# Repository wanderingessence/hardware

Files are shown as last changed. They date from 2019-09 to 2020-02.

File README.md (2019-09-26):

# hardware
Altium repository for pod V. This project is set up to provide all documentation, design and data validation required for the Badgerloop Pod V PCBs. This repository builds off of our previous work the podiv-altium repository. 

## Prerequisites
Altium only works on Windows. See  [Altium System Requirements](https://www.altium.com/documentation/18.0/display/ADES/Altium+Designer+-+((System+Requirements))") for more information. An internet connection is required to connect to the license server and dual monitors are nice to have. Microsoft Excel is required for BOM generation.

## Installation
1. Contact Ezra Boley, Shelby Riggleman or Ryan Castle to be added to the Badgerloop Team AltiumLive Account and the Badgerloop [Github](https://github.com/badgerloop-software"). You will receive an email from Altium with your account information. You may continue to step to step 8 without requiring an active license. If there is a delay for some reason, you can work on Altium training and practice on CAE computers or through [Citrix](https://remote.engr.wisc.edu/vpn/index.html), but we are usually able to add new users within 24 hours. CAE currently runs Altium 16, which has similar features but has a different interface and some bugs. Badgerloop currently supports Altium 19.0.10. 
2. Download the latest version of [Altium Designer](https://www.altium.com/products/downloads) 
3. Install Altium. Default file paths will work.
4. Insall [Git Bash](https://gitforwindows.org/") Git Bash (or whatever BASH emulation tool you are comfortable with)
5. Open Git Bash
6. Type the following commands into the command prompt window:
   + cd ../..
   + mkdir git
   + cd git
   + git clone https://github.com/badgerloop-software/hardware.git
   + cd hardware
   + git checkout -b <your-username_training>
   + Open Altium and sign in. You are now on a training branch that you will complete your first getting started project on if you are new to Altium. 
7. Go to User (Silhouette in the top right corner) -> License Management. Then Click Sign In and enter your username and password associated with Altium Live and accept the warning. It's also a good idea to check Sign me in when I start Altium Designer if you'd like to save a little time.

_NOTE: If you go click "Sign In" directly from User, you will be asked for a server address. This is not what you want. Go back to step 7 and hit License Management instead of Sign In._ 

8. Click Use to claim a license. If you are not using a valid license, you will be able to view files in Altium Designer but you will not be able to make edits. Ensure that you are choosing an Altium Designer License and not our PDN License. That's something else. 
9. You are now ready to use Altium. See [Training](#training) for more details on how to get started. 

## Training
+ View the [Badgerloop Altium Presentation](https://uwmadison.box.com/s/2sdt8kfaeyde04sg8edn62u7vtrdsiyx") for a getting started project. You can work locally for this project. Git-specific training will be posted at a later date. 
+ If you are new to using Git, read through the [Altium Git Guide](https://uwmadison.app.box.com/file/324684243638) which provides some common commands to get you started. 
+ Multivibrator Project: The Multivibrator Project from Altium is hands down the best training resource for getting started with Altium. We ask that everyone new to PCB design complete this tutorial on their own prior to working on Badgerloop schematics or boards. While we want to help everyone as much as possible, it's on you to get a bit of a background. Feel free to ask Ezra, Shelby or Ryan if you have any issues with the tutorial. [Multivibrator Tutorial] (https://www.altium.com/documentation/18.0/display/ADES/From+Idea+to+Manufacture+-+Driving+a+PCB+Design+through+Altium+Designer). This guide goes "From Idea to Manufacture" and drives a design all the way though rough-drawing your circuit, making library symbols and footprints, schematic capture, placement, layout, and routing, as well as manufacturing outputs. 

## Github Basics
TODO @Kevin 

## Acknowledgements
+ [Altium](www.altium.com), for being an amazing sponsor! 
+ Dave Jones of the EEVBlog, as we'd have no idea what we were doing without his videos.

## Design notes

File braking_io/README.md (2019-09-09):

# Purpose
The Braking IO board (generically called Remote IO or RIO boards) are responsible for managing the sensors and actuators on each of the braking trays. Previously, we routed several dozen wire harnesses across the majority of the pod in order to connect to the pressure sensors and solenoids. This board reduces all of that routing into a single power harness, UART + Heartbeat cable and allows for more localized routing to each of the sensors and actuators on the tray. Eventually, there will be 2 of these boards on the pod; one for each braking tray

# Requirements
* Mechanical:
   * Board shall have at least four 4-40 mounting holes
   * Board shall fit in the mechanical enclosure
   * Bonus: Board shall contain at least three fiducals for potential automated assembly
* Connector Interface: 
   * Connectors shall be properly rated for voltage and current
   * Connectors shall have a positive locking feature
   * Connectors shall share a common pinout and be polarized
   * connectors shall be kept to a minimum
   * Bonus: System shall be designed for 1:1 harnesses in order to use off the shelf cable assemblies as much as possible. 
   * Bonus: Harness ID pin shall be added to each connector in order to detect if each cable is properly connected or not. 
* Power:
   * Fusing: Bus input shall be fused to protect against over-current events
   * Telemetry: All rails shall have voltage and current sensing
   * Filtering: Bus voltage shall be filtered
   * Rails: 5V and 3V Rails shall be implemented
* Sensors:
   * Pressure: Pressure telemetry inputs (8x) shall be configurable for both voltage and current output pressure transducers
   * Temperature: Two configurable board mount or external temperature sensors shall provide temperature feedback
* Actuators:
  * Solenoids: 8x solenoid driver circuits shall be implemented
  * Bonus: Use the MPQ6610 instead of a traditional N-MOS driver to save on power
  * Bonus: LEDs on each solenoid
* Watchdog:
  * Board shall have a way to reset all solenoids in case of loss of heartbeat or UART connection from either the microcontroller or the primary flight computer
* MCU:
  * Board shall be capable of sending telemetry, over UART, to the primary flight computer
  * Board shall be capable of receiving commands to actuate different valves, over UART, from the primary flight computer
  
# Info
* Schematic Designers @btobin @rcastle1
* Layout: @btobin
* Need-by-date: 10/1/2019

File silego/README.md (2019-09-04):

# Silego Designs
See https://www.dialog-semiconductor.com/gpio-expander 

## Silego Basics
These chips are configurable mixed-signal devices that allow the user to connect various gates, LUTs, delays, comparators, etc. to create unique, custom hardware logic with fewer external components and rapid iteration. These are pretty neat chips. 

To get started, download GreenPAK Designer https://www.dialog-semiconductor.com/greenpak-designer-software and open a sample .gp* project and check out a reference design

We also have a development and programming board that allows us to test out the circuit in the real-world before committing to a design. If you've taken ECE 352 or ECE 551, you know how important it is to simulate and test your programmable hardware before committing. With an un-programmed part, you can simulate and update your image as much as you'd like, but as soon as you flash the Non-Volatile Memory, that chip cannot be re-programmed. We have a limited amount of components, so we want to make sure we are confident in our design before burning an IC, but know we have the flexibility to adjust even after PCBs have gone out to fabrication or assembly.

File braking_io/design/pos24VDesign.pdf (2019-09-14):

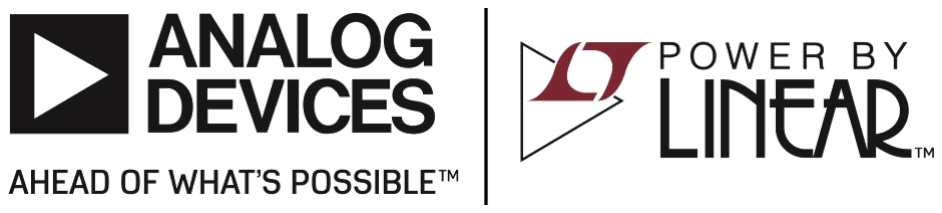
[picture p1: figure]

Printed : 09/14/2019 | Copyright © 2014 Analog Devices Inc.

## Designer : Castle

## Project Date : 9/14/2019

## Project Name : LTC3114-1 24V Supply

## Output Rails : Vout1 = 24.09V / 0.5A (max.)

## Vin : 18V (min.), 24V (nom.), 30V (max.)

# LTC3114-1 Supply Design Summary Report

## Output Rails : Vout1 = 24.09V / 0.5A (max.)

## Vin : 18V (min.), 24V (nom.), 30V (max.)

## LTC3114-1 Solution - Simplified Schematic

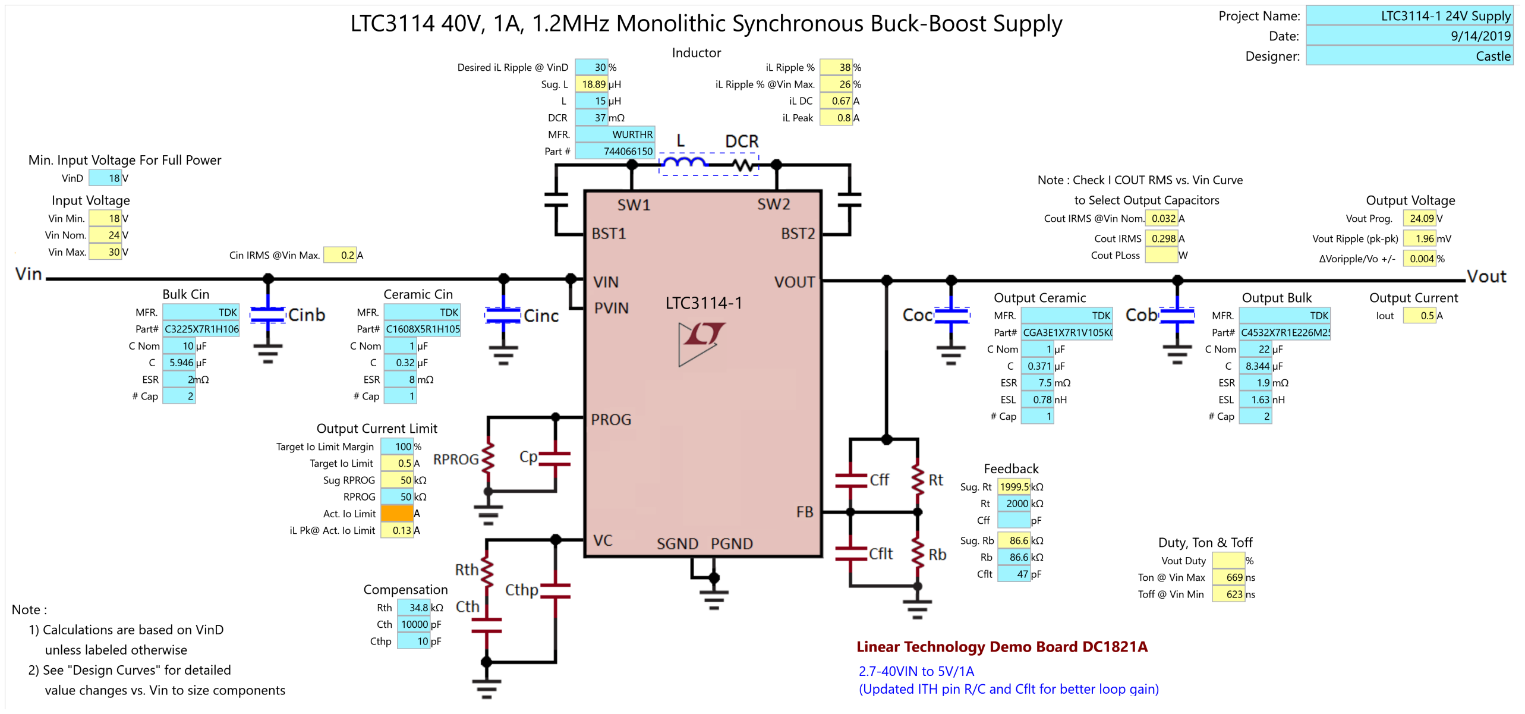
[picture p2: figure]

## Rail # 1 : Vin = 24V, Vout1 = 24.09V

## LTC3114-1 Solution - Efficiency & Loss Estimations

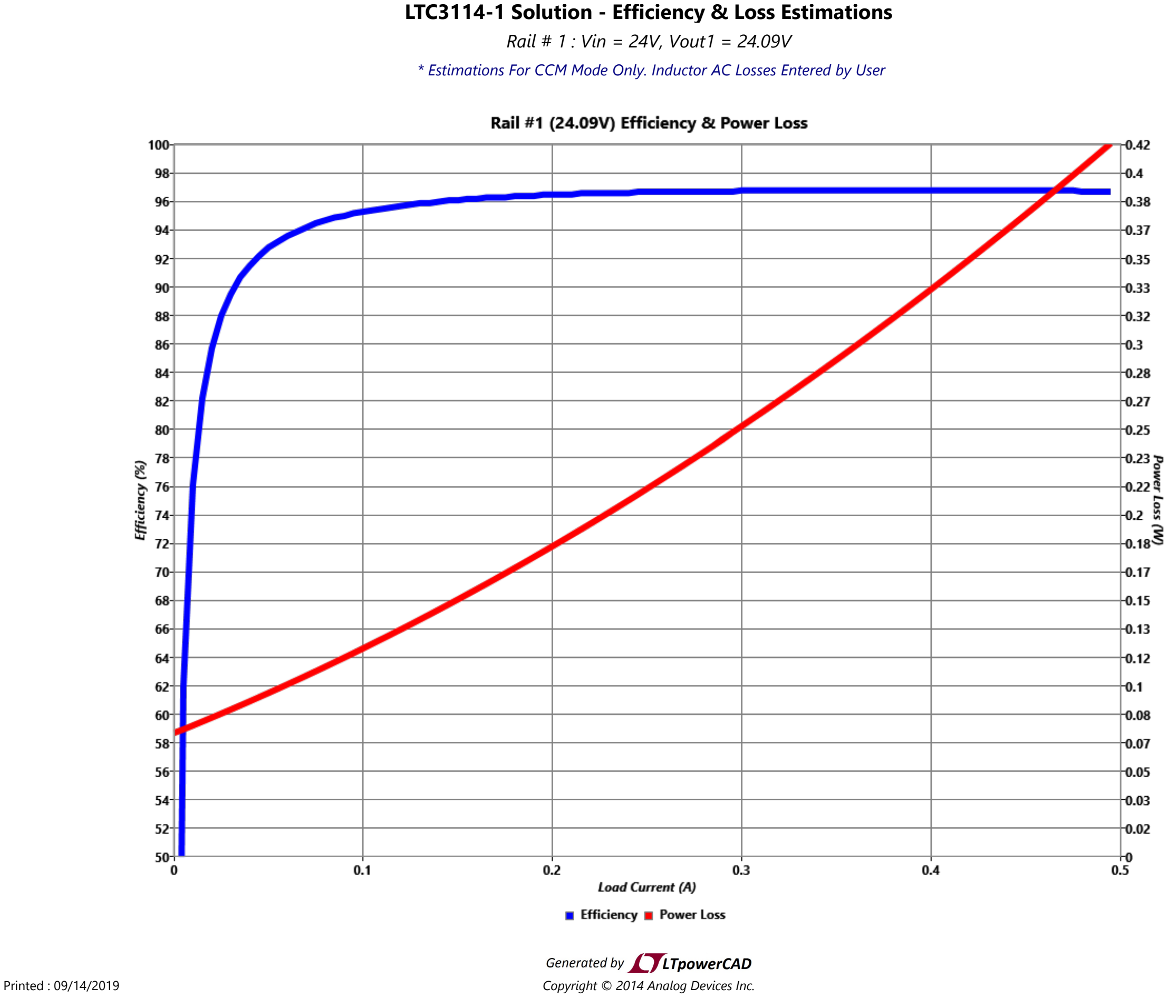
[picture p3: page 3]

### * Estimations For CCM Mode Only. Inductor AC Losses Entered by User

### * Estimations For CCM Mode Only. Estimations Based On Small Signal Avg. Model

## Rail # 1 : Vin = 24V, Vout1 = 24.09V, Iout1 = 0.5A

## LTC3114-1 Solution - Loop Gain & Load Transient Estimations

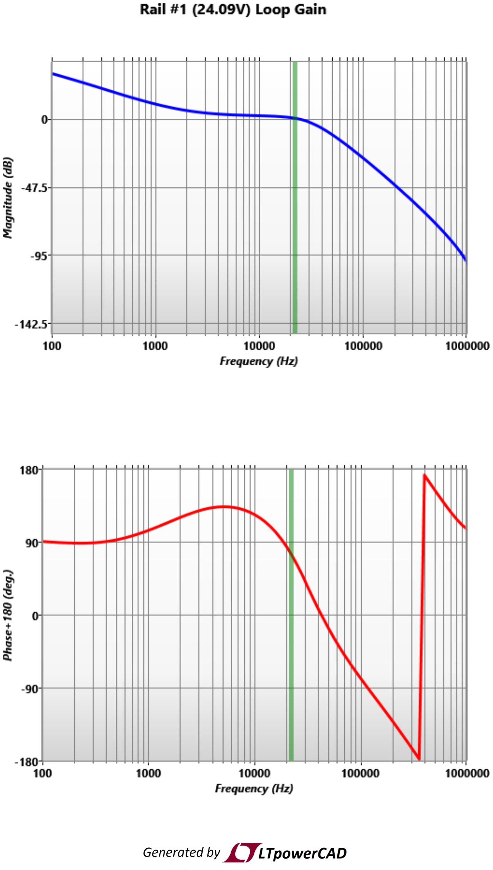
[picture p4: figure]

## LTC3114-1 Solution - Summary

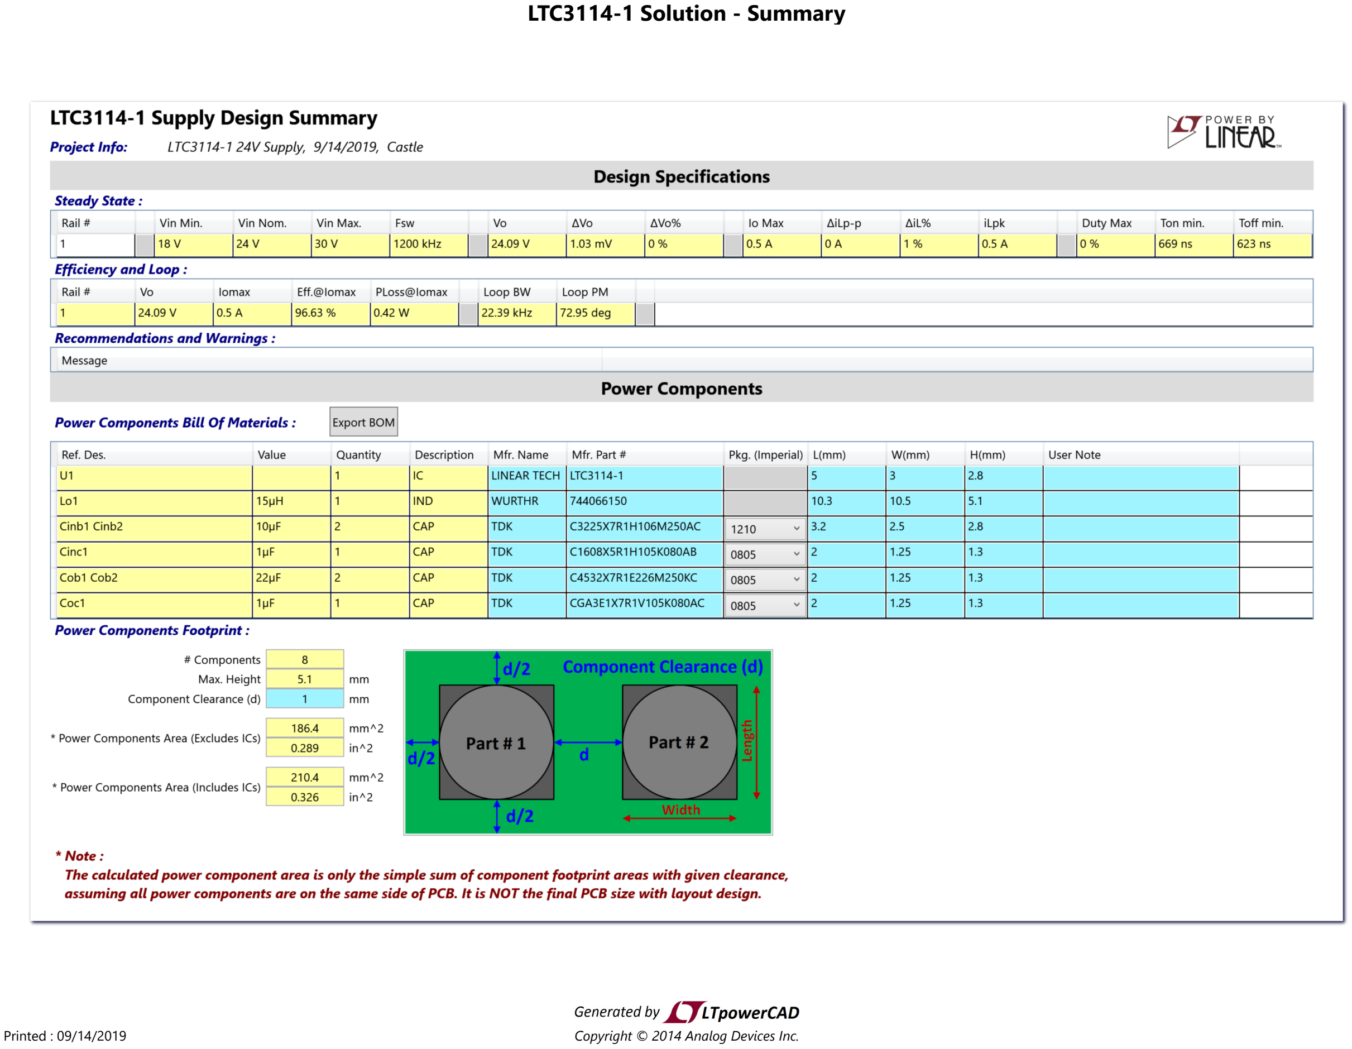
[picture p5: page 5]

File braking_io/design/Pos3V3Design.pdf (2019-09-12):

TPS5420 3.3V Supply Design

Design Parameters
Vin_min≔8 V | Vin_ripple≔300 mV
Vin_max≔35 V | Vout_ripple≔50 mV
Vout_nom≔3.3 V | Iout_max≔2 A
K_ind≔0.2 | Fsw≔500 kHz | Fsw fixed by TPS5420

Input Capacitors

C_bulk≔10 ⋅ 10⁻⁶ F | ESRmax≔0.002086 Ω | ESL_max≔1200 ⋅ 10⁻⁹ H
Vin_ripple_calc≔Iout_max⋅―――――+ | =
| 0.25
| C_bulk⋅Fsw

((Iout_max⋅ESRmax)) 0.104 V

I_cin≔――――=

Iout_max
2
1 A | Choose input capacitors rated for at
least 50V with a ripple current capacity for each at 3A at 500kHz

Output Filter Components

Inductor Selection

L_min≔Vout_nom⋅―――――――――――――=

| ((Vin_max-Vout_nom))
((Vin_max)) ⋅K_ind⋅ Iout_max⋅Fsw⋅ 0.8
| | ⎛⎝1.868 ⋅ 10⁻⁵⎞ ⎠ H

L_nom≔18 ⋅ 10⁻⁶ H

I_L_rms≔ | | =

⎛
⎜
⎝

Iout_max⋅ Iout_max+―1

| 12 ⎛ ⎜
⎝――――――――――――

((Vout_nom⋅ ((Vin_max-Vout_nom)))) ((Vin_max⋅L_nom⋅Fsw⋅ 0.8))

⎞
⎟
⎠

2 ⎞
⎟
⎠

0.5
2.001 A
I_L_peak≔ | =

⎛
⎜
⎝
| Iout_max+―Vout_nom ―――⋅ ――――――――

((Vin_max-Vout_nom))
1.6 ⋅Vin_max⋅L_nom⋅Fsw

⎞
⎟
⎠

2.113 A

| Choose an inductor with at least 2.5A rms and 3A

saturation current

Output Capacitor Selection

Created with PTC Mathcad Express. See www.mathcad.com for more information.

Fco≔10 kHz Target Crossover frequency

Cout≔――――――――――=

1
((3357 ⋅L_nom⋅Fco ⋅Vout_nom))

⎛⎝2.735 ⋅ 10⁻⁴⎞

⎠ ―s ―⋅ ―

### 6 A

3
kg ⋅

### 2 m

4
~100uF

Nc≔5 Select 5x 22uF capacitors to approximate 100uF

Cout_esr_max≔――――――=

1
((2 ⋅π⋅Cout⋅Fco))

0.058 ―kg―⋅ ―

### 2 m

4
s ⋅

### 5 A

3
~88mOhms

Vpp_max≔Cout_esr_max⋅Vout_nom⋅――――――――――=

((Vin_max-Vout_nom))
Nc ⋅Vin_max⋅L_nom⋅Fsw⋅ 0.8

0.003 ―kg―⋅ ―

### 2 m

4
s ⋅

### 5 A

2

6mV pk-pk ripple

Ensure output cap is rated for Vout + 1/2 ripple voltage + derating, ~ 5.006*1.3=6.5V, round up to 25V

Estimate ripple current max at 150mA

Output Voltage Set

R1≔10 kΩ | R1_min≔R1 ⋅.999 | R1_max≔R1 ⋅ 1.001

R2≔――――――――=

R1 ⋅ 1.221
((Vout_nom-1.221 V))
| ⎛⎝5.873 ⋅ 10³ ⎞

⎠ ―1
A
| | 5.75KOhms +/-0.1%
R2_min≔R2 ⋅.999 | R2_max≔R2 ⋅ 1.001
Vout_min≔R1_min⋅―――+ | =
| 1.221 R2_max 1.221 V 3.296 V
Vout_max≔R1_max⋅―――+ | =
| 1.221 R2_min 1.221 V 3.304 V

Boot Cap

Datasheet gives 0.01uF for the boot capacitor. NP0/COG preferred

Duty Cycle (Max)

D_max≔――――=

Vout_nom
Vin_min⋅η
η≔0.9 | D_min≔――――= | 0.458 Vout_nom
Vin_max⋅η

0.105

Catch Diode
D_reverse_voltage_min≔Vin_max+0.5 V =35.5 V

D_iout_max≔Iout_max+0.5 ⋅ I_L_rms=3.001 A
Diodes, Inc B340A has a reverse voltage of 40V, forward current of 3A and forward voltage drop of 0.5V
If≔Iout_max⋅ ((1- D_min))=1.79 A If_2≔Iout_max⋅ ((1- D_max))=1.083 A

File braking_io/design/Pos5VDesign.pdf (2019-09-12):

TPS5420 5V Supply Design

Design Parameters
Vin_min≔10 V | Vin_ripple≔300 mV
Vin_max≔35 V | Vout_ripple≔50 mV
Vout_nom≔5 V | Iout_max≔2 A
K_ind≔0.2 | Fsw≔500 kHz | Fsw fixed by TPS5420

Input Capacitors

C_bulk≔10 ⋅ 10⁻⁶ F | ESRmax≔0.002086 Ω | ESL_max≔1200 ⋅ 10⁻⁹ H
Vin_ripple_calc≔Iout_max⋅―――――+ | =
| 0.25
| C_bulk⋅Fsw

((Iout_max⋅ESRmax)) 0.104 V

I_cin≔――――=

Iout_max
2
1 A | Choose input capacitors rated for at
least 50V with a ripple current capacity for each at 3A at 500kHz

Output Filter Components

Inductor Selection

L_min≔Vout_nom⋅―――――――――――――=

| ((Vin_max-Vout_nom))
((Vin_max)) ⋅K_ind⋅ Iout_max⋅Fsw⋅ 0.8
| | ⎛⎝2.679 ⋅ 10⁻⁵⎞ ⎠ H

L_nom≔33 ⋅ 10⁻⁶ H

I_L_rms≔ | | =

⎛
⎜
⎝

Iout_max⋅ Iout_max+―1

| 12 ⎛ ⎜
⎝――――――――――――

((Vout_nom⋅ ((Vin_max-Vout_nom)))) ((Vin_max⋅L_nom⋅Fsw⋅ 0.8))

⎞
⎟
⎠

2 ⎞
⎟
⎠

0.5
2.002 A
I_L_peak≔ | =

⎛
⎜
⎝
| Iout_max+―Vout_nom ―――⋅ ――――――――

((Vin_max-Vout_nom))
1.6 ⋅Vin_max⋅L_nom⋅Fsw

⎞
⎟
⎠

2.162 A

| Choose an inductor with at least 2.5A rms and 3A

saturation current

Output Capacitor Selection

Created with PTC Mathcad Express. See www.mathcad.com for more information.

Fco≔10 kHz Target Crossover frequency

Cout≔――――――――――=

1
((3357 ⋅L_nom⋅Fco ⋅Vout_nom))

⎛⎝1.805 ⋅ 10⁻⁴⎞

⎠ ―s ―⋅ ―

### 6 A

3
kg ⋅

### 2 m

4
~100uF

Nc≔5 Select 5x 22uF capacitors to approximate 100uF

Cout_esr_max≔――――――=

1
((2 ⋅π⋅Cout⋅Fco))

0.088 ―kg―⋅ ―

### 2 m

4
s ⋅

### 5 A

3
~88mOhms

Vpp_max≔Cout_esr_max⋅Vout_nom⋅――――――――――=

((Vin_max-Vout_nom))
Nc ⋅Vin_max⋅L_nom⋅Fsw⋅ 0.8

0.006 ―kg―⋅ ―

### 2 m

4
s ⋅

### 5 A

2

6mV pk-pk ripple

Ensure output cap is rated for Vout + 1/2 ripple voltage + derating, ~ 5.006*1.3=6.5V, round up to 25V

Estimate ripple current max at 150mA

Output Voltage Set

R1≔10 kΩ | R1_min≔R1 ⋅.999 | R1_max≔R1 ⋅ 1.001

R2≔――――――――=

R1 ⋅ 1.221
((Vout_nom-1.221 V))
| ⎛⎝3.231 ⋅ 10³ ⎞

⎠ ―1
A
| | 3.24KOhms +/-0.1%
R2_min≔R2 ⋅.999 | R2_max≔R2 ⋅ 1.001
Vout_min≔R1_min⋅―――+ | =
| 1.221 R2_max 1.221 V 4.992 V
Vout_max≔R1_max⋅―――+ | =
| 1.221 R2_min 1.221 V 5.008 V

Boot Cap

Datasheet gives 0.01uF for the boot capacitor. NP0/COG preferred

Duty Cycle (Max)

η≔0.9 D_min≔――――= Vout_nom Vin_max⋅η
0.159 D_max≔――――=

Vout_nom
Vin_min⋅η

0.556

Catch Diode
D_reverse_voltage_min≔Vin_max+0.5 V =35.5 V

D_iout_max≔Iout_max+0.5 ⋅ I_L_rms=3.001 A
Diodes, Inc B340A has a reverse voltage of 40V, forward current of 3A and forward voltage drop of 0.5V
If≔Iout_max⋅ ((1- D_min))=1.683 A If_2≔Iout_max⋅ ((1- D_max))=0.889 A

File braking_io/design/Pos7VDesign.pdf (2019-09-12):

TPS5420 7V Supply Design

Design Parameters
Vin_min≔10 V | Vin_ripple≔300 mV
Vin_max≔35 V | Vout_ripple≔50 mV
Vout_nom≔7 V | Iout_max≔2 A
K_ind≔0.2 | Fsw≔500 kHz | Fsw fixed by TPS5420

Input Capacitors

C_bulk≔10 ⋅ 10⁻⁶ F | ESRmax≔0.002086 Ω | ESL_max≔1200 ⋅ 10⁻⁹ H
Vin_ripple_calc≔Iout_max⋅―――――+ | =
| 0.25
| C_bulk⋅Fsw

((Iout_max⋅ESRmax)) 0.104 V

I_cin≔――――=

Iout_max
2
1 A | Choose input capacitors rated for at
least 50V with a ripple current capacity for each at 3A at 500kHz

Output Filter Components

Inductor Selection

L_min≔Vout_nom⋅―――――――――――――=

| ((Vin_max-Vout_nom))
((Vin_max)) ⋅K_ind⋅ Iout_max⋅Fsw⋅ 0.8
| | ⎛⎝3.5 ⋅ 10⁻⁵⎞ ⎠ H

L_nom≔36 ⋅ 10⁻⁶ H

I_L_rms≔ | | =

⎛
⎜
⎝

Iout_max⋅ Iout_max+―1

| 12 ⎛ ⎜
⎝――――――――――――

((Vout_nom⋅ ((Vin_max-Vout_nom)))) ((Vin_max⋅L_nom⋅Fsw⋅ 0.8))

⎞
⎟
⎠

2 ⎞
⎟
⎠

0.5
2.003 A
I_L_peak≔ | =

⎛
⎜
⎝

Iout_max+―Vout_nom ―――⋅ ――――――――

| ((Vin_max-Vout_nom)) 1.6 ⋅Vin_max⋅L_nom⋅Fsw ⎞ ⎟ ⎠
2.194 A
| Choose an inductor with at least 2.5A rms and 3A saturation current

Output Capacitor Selection

Fco≔10 kHz Target Crossover frequency

Cout≔――――――――――=

| 1
((3357 ⋅L_nom⋅Fco ⋅Vout_nom))
| ⎛⎝1.182 ⋅ 10⁻⁴⎞ ⎠ ―s ―⋅ ― 6 A

3
| kg ⋅ 2 m

4

Created with PTC Mathcad Express. See www.mathcad.com for more information.

~100uF

Nc≔5 Select 5x 22uF capacitors to approximate 100uF

Cout_esr_max≔――――――=

1
((2 ⋅π⋅Cout⋅Fco))

0.135 ―kg―⋅ ―

### 2 m

4
s ⋅

### 5 A

3
~88mOhms

Vpp_max≔Cout_esr_max⋅Vout_nom⋅――――――――――=

((Vin_max-Vout_nom))
Nc ⋅Vin_max⋅L_nom⋅Fsw⋅ 0.8

0.01 ―kg―⋅ ―

### 2 m

4
s ⋅

### 5 A

2

6mV pk-pk ripple

Ensure output cap is rated for Vout + 1/2 ripple voltage + derating, ~ 5.006*1.3=6.5V, round up to 25V

Estimate ripple current max at 150mA

Output Voltage Set

R1≔10 kΩ | R1_min≔R1 ⋅.999 | R1_max≔R1 ⋅ 1.001

R2≔――――――――=

R1 ⋅ 1.221
((Vout_nom-1.221 V))
| ⎛⎝2.113 ⋅ 10³ ⎞

⎠ ―1
A
| | 1.8KOhms +/-0.1%
R2_min≔R2 ⋅.999 | R2_max≔R2 ⋅ 1.001
Vout_min≔R1_min⋅―――+ | =
| 1.221 R2_max 1.221 V 6.988 V
Vout_max≔R1_max⋅―――+ | =
| 1.221 R2_min 1.221 V 7.012 V

Boot Cap

Datasheet gives 0.01uF for the boot capacitor. NP0/COG preferred

Duty Cycle (Max)

η≔0.9 D_min≔――――= Vout_nom Vin_max⋅η
0.222 D_max≔――――=

Vout_nom
Vin_min⋅η

0.778

Catch Diode
D_reverse_voltage_min≔Vin_max+0.5 V =35.5 V

D_iout_max≔Iout_max+0.5 ⋅ I_L_rms=3.002 A
Diodes, Inc B340A has a reverse voltage of 40V, forward current of 3A and forward voltage drop of 0.5V
If≔Iout_max⋅ ((1- D_min))=1.556 A If_2≔Iout_max⋅ ((1- D_max))=0.444 A

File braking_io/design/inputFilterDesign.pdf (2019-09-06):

## Input filter design for switching power supply:

Written by Michele Sclocchi michele.sclocchi@nsc.com
Application Engineer
National Semiconductor

Basic step-down simple switcher power supply:

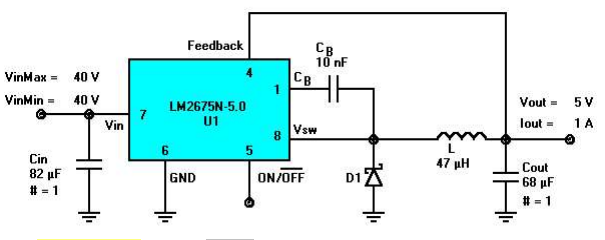
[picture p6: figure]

Input parameters | Results
-Maximum input voltage: | Vinput | 35V :=
-Output current: | Iout | 10 A :=
-Output voltage: | Vout | 5V :=

-Output inductor:

inductance: | Lo | 33 := μH
DC resistance: | RL := 0.088Ω
-Output capacitor: | Co | 68 := μF
ESR | 0.09 := | Ω
-Duty cycle: | D | 0.458 :=
-Output impedance: | Ro

Vout
Iout
:= | Ro 0.5 A- 2

kg s- 3
m

2
= | | |
i | 1 2000 := .. | f
i

100

( ) i 200 -
500
:=

w
i
| f i

rad
s
:= | s i

2πj w
i

:=

1

-Input impedance of the power supply:

Zii

Ro R + L

D

2

### 1 si

Lo
Ro R + L

ESR

Ro R L
Ro R + L

+

+ | Co
+ | s( )i
2
LoCo

Ro ESR +
Ro R + L
+ |

### 1 si

+ ( | ) Ro ESR + | Co
:= |

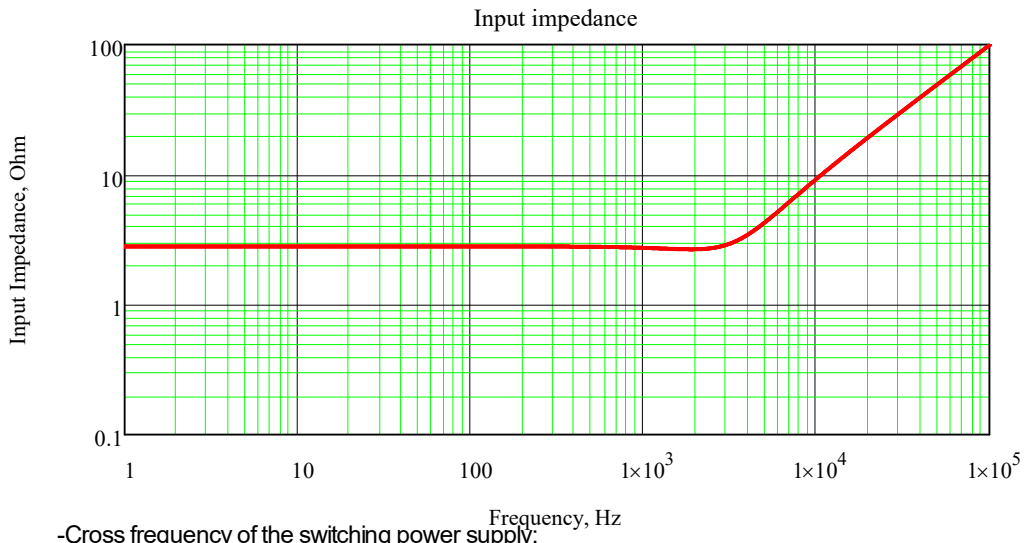
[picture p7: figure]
Input impedance; Frequency, Hz Input Impedance, Ohm

-Cross frequency of the switching power supply:

Fcross 32kHz :=

To meet the noise filtering requirements the input filter has to have the corner frequency around one decade below the bandwidth of the feed back loop of the power supply.

-Cut of frequency of the input filter: | fc | 5kHz :=
-Cut off frequency in radiant: | ωc | fc 2 := π ωc 3.142 104
- s
- 1
= |
-Maximum input impedance of the power supply: | Rin | 25 ohm :=
-Input Capacitance of the power supply: | C := 15μF

2

### - UNDUMPED LC FILTER:

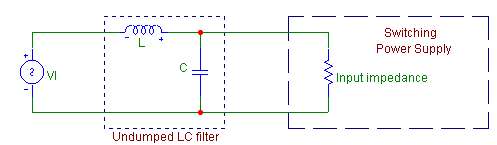
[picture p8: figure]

-Inductance calculated:

L

1

ωc

2C

:= | L 67.547 = | μH

-Damping factor:

ζ

L
2 Rin | L C
:= | ζ = 0.042

-Inductor used:
Lf | 1 := μH
Rf | 0.030 := | Ω

-Capacitor used:

Cf | 33 := μF
ESRci | 0.150 := | Ω

-Cut off frequency of the filter:

fcfilter1

1
2π Lf Cf
:= | fcfilter1 = 27.705 kHz

-Transfer function:

Z1i

Rf si

:= + Lf

Z2i

ESRci 1
s
i

Cf

:= +

Z2eqi

Z2i

Rin

Z2i

+ Rin

:=

Filteri

### 20 log

Z2eqi

Z2eqi

Z1i

+

:=

3

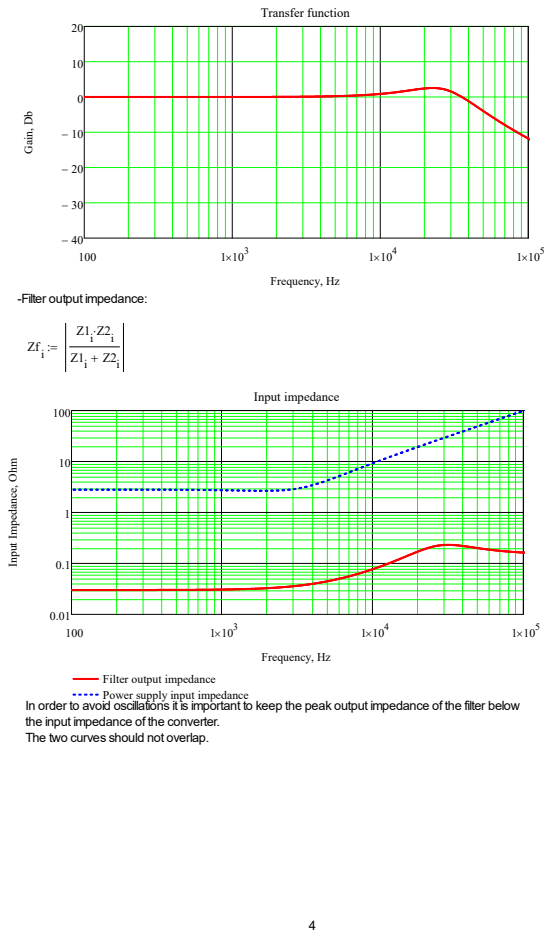
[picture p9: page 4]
Transfer function; Zfi; Input impedance

Frequency, Hz Gain, Db

-Filter output impedance:

Frequency, Hz Input Impedance, Ohm

Filter output impedance
Power supply input impedance

In order to avoid oscillations it is important to keep the peak output impedance of the filter below
the input impedance of the converter.
The two curves should not overlap.

### -PARALLEL DAMPED FILTER:

In most of the cases a parallel damped filter meet easily the damping and impedance requirements.

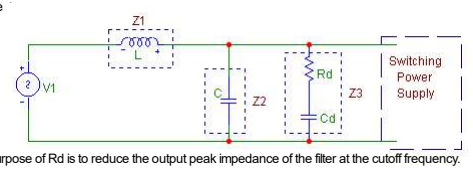
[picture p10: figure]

The purpose of Rd is to reduce the output peak impedance of the filter at the cutoff frequency. The capacitor Cd blocks the DC component of the input voltage.

-Damping resistance:

Rd | Lf Cf
:= | Rd 0.174 A- 2

kg s- 3
m

2
= | | |
Cd | 4 Cf := | Cd 132 = | μF
ESRcd | 0.200 := | Ω

Z3i

1
s
i

Cd

:= + ESRcd + Rd

Z3eq2i

Z2eqi

Z3i

Z2eqi

Z3i

+

:=

-Transfer function:

Filter2i

### 20 log

Z3eq2i

Z3eq2i

Z1i

+

:=

5

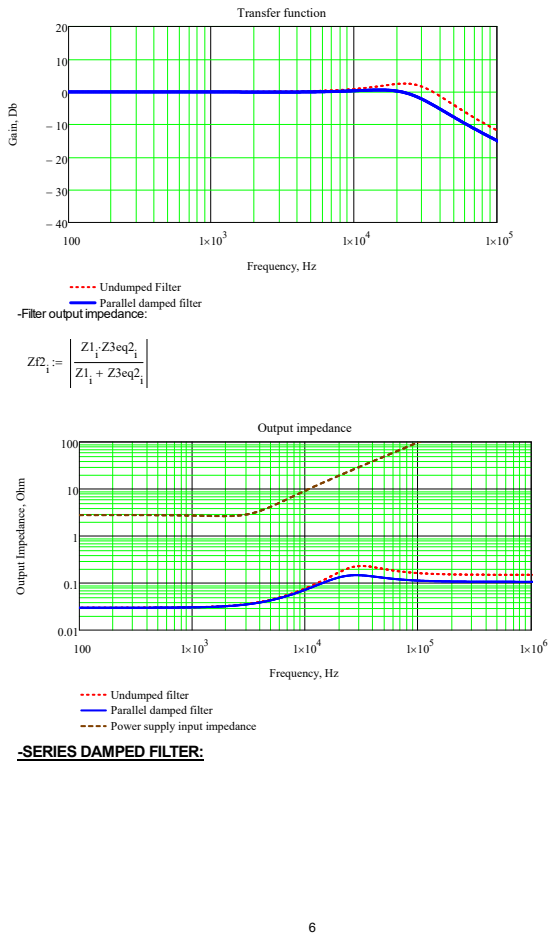
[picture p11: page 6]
Transfer function; Output impedance

Frequency, Hz Gain, Db

Undumped Filter
Parallel damped filter

-Filter output impedance:

Frequency, Hz Output Impedance, Ohm

Undumped filter
Power supply input impedance

-SERIES DAMPED FILTER:

sr

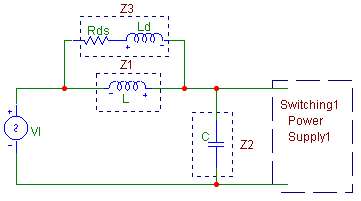
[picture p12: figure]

1
2π Lf Cf

:=

-Series inductor: | n3

2
15

:=

Ld | Lf n3
:= | | Ld 0.133 = | μH

-Series damping resistance:

Rds Lf
Cf
:= | Rds 0.174 A- 2

kg s- 3
m

2
= | | |

Z3si

Rds si

:= + Ld

Z13i

Z1i

Z3si

Z1i

Z3si

+

:=

-Transfer function:

Filter3i

### 20 log

Z2i

Z2i

Z13i

+

:=

7

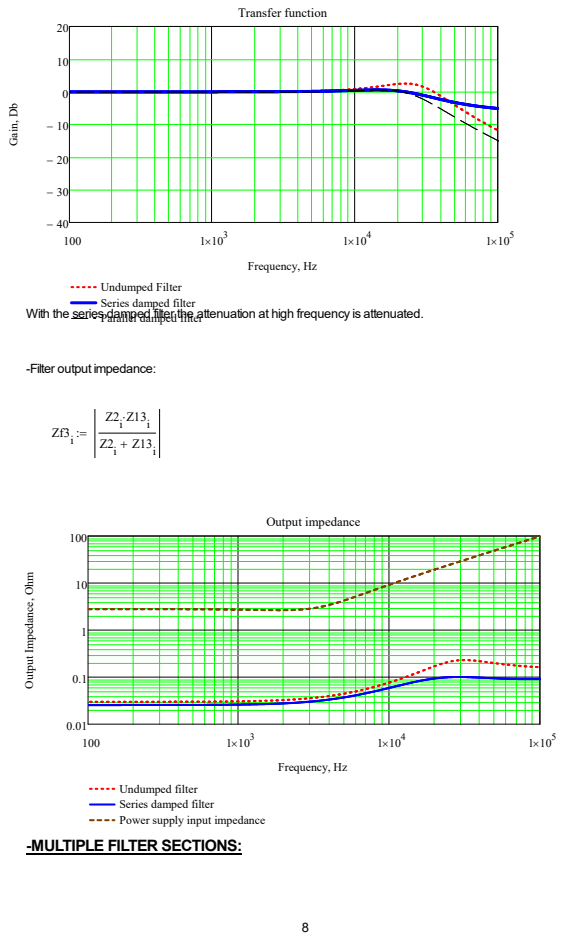
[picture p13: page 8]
Transfer function; Output impedance

Frequency, Hz Gain, Db

Undumped Filter
Series damped filter
Parallel damped filter

With the series damped filter the attenuation at high frequency is attenuated.

-Filter output impedance:

Frequency, Hz Output Impedance, Ohm

Undumped filter
Power supply input impedance

-MULTIPLE FILTER SECTIONS:

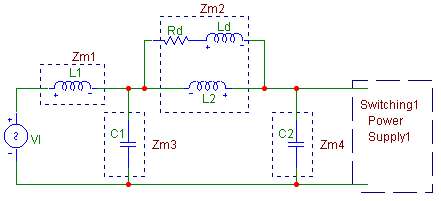
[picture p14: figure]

-First LC filter:

L1

Lf
4
:= | L1 0.25 = | μH | RL1 | 0.1 := | Ω

C1

Cf
4
:= | C1 8.25 = | μF | ESRc1 | 0.120 := | Ω
fm1 | 1
2π L1 C1
:= | fm1 110.821 kHz = |

-Second LC filter:
L2 | 7 L1 := | L2 1.75 = | μH | RL2 | 0.1 := | Ω
C2 | 4 C1 := | C2 33 = μF | ESRc2 | 0.120 := | Ω
fm2 | 1
2π L2 C2
:= | fm2 20.943 kHz = |
Rd4 | L1 C2
:= | Rd4 0.087 A- 2

kg s- 3
m

2
= | | |
Ld4 | L1
8

:=

Zm1i

s
i
:= L1 + RL1 | Zm2i

1
s
i

C1

:= + ESRc1

Zm3i

Rd4 si

+ Ld4 ( | ) s
i
L2 + RL2 ( | )

Rd4 si

+ Ld4 ( | ) s
i

+ L2 + RL2

:= | Zm4i

1
s
i

C2

:= + ESRc2

-Transfer function:

9

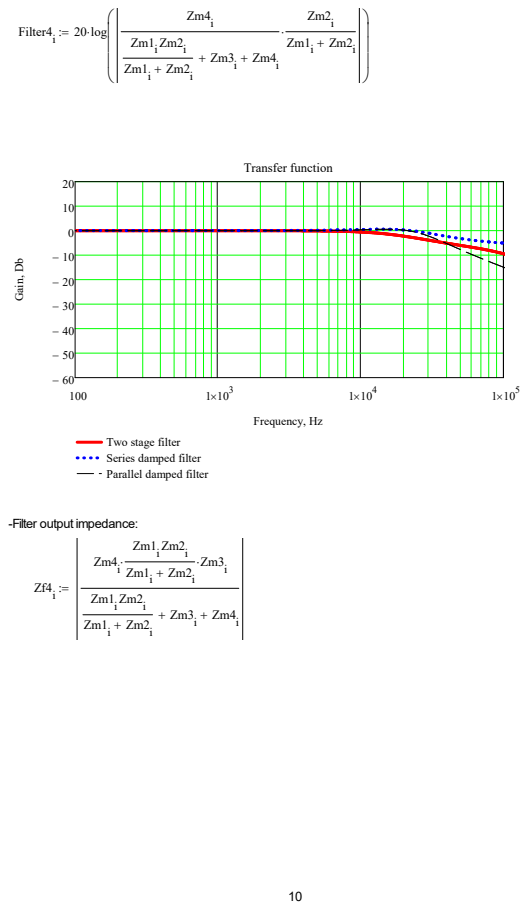
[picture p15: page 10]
Filter4i; 20 log; Transfer function

Frequency, Hz Gain, Db

Two stage filter
Series damped filter
Parallel damped filter

-Filter output impedance:

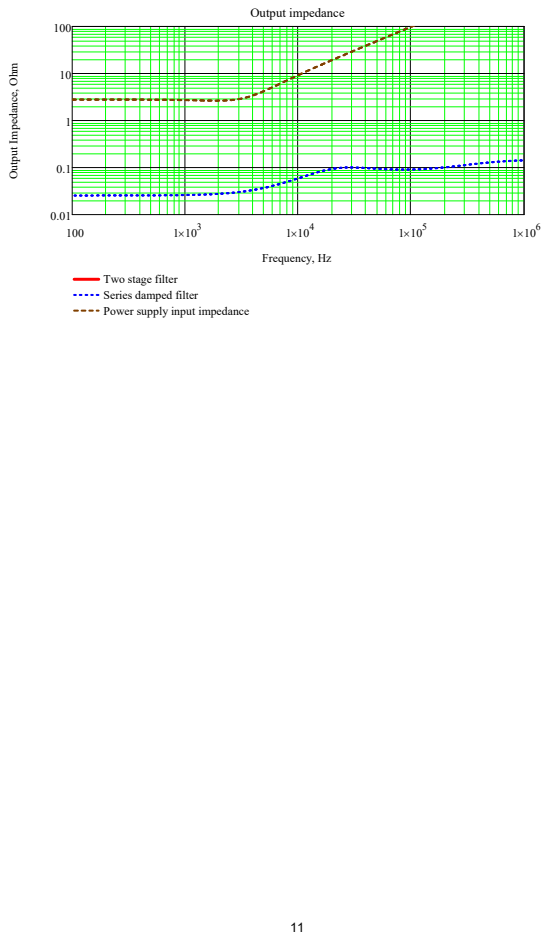
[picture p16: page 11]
Output impedance

Frequency, Hz Output Impedance, Ohm

Two stage filter
Series damped filter
Power supply input impedance

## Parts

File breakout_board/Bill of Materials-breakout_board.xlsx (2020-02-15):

Comment | Description | Designator | Footprint | LibRef | Quantity
4-40 Mount Hole |  | MH1, MH2 | MH | 4-40 Mount Hole | 2
43045-2400 | Molex MICRO-FIT 3.0 Series, Series Number 43045, 3mm Pitch 24 Way 2 Row Right Angle PCB Header, Solder Termination, 5A | P1 | 430452400 | 43045-2400 | 1
43045-2412 | HEADER, VERTICAL, 24WAY; Series:Micro-Fit 3.0; Pitch Spacing:3mm; Contact Termination Type:Through Hole; No. of Contacts:24; No. of Rows:2; Connector Mounting:PCB; Gender:Plug; Contact Material:Brass; Contact Plating:Tin; ;RoHS Compliant: Yes | P2 | 0430452412 | 43045-2412 | 1

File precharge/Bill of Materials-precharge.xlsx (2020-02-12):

Comment | Description | Designator | Footprint | LibRef | Digi-Key Part Number | Manufacturer P/N | Manufacturer Part Number | Quantity
CGA9P4X7T2W105K250KE_1 | CAP CER 1UF 450V X7T 2220 | C1, C2, C3 | CAPC5860X28N | CGA9P4X7T2W105K250KE_1 |  |  | CGA9P4X7T2W105K250KE | 3
Diode General Purpose_2 | DIODE GEN PURP 20V 350MA SOD323 | D1, D2, D3 | SODFL250X110-2N | Diode General Purpose_2 |  | SD103CWS-7-F |  | 3
F6257CT-ND | FUSE BOARD MNT 500MA 350VAC/VDC | F1 | SMD-0805-RES | F6257CT-ND |  | 46205000000 |  | 1
F6257CT-ND | FUSE BOARD MNT 500MA 350VAC/VDC | F2, F3 | FUSE BOARD MNT 500MA 350VAC/VDC | F6257CT-ND |  | 46205000000 |  | 2
TP | SMD TEST POINT | HV_POS, TP1, TP2, TP5, TP6, TP7 | Test Point | TP |  |  |  | 6
SRR3818A-1R0Y | FIXED IND 1UH 3.6A 37 MOHM SMD | I1 | INDM3838X18N | SRR3818A-1R0Y |  | SRR3818A-1R0Y |  | 1
744309033 | FIXED IND 330NH 47.5A 0.165 MOHM | I2 | INDM140130X90N | 744309033 |  | 744309033 |  | 1
Gigavac 200 |  | K1 | Gigavac 200 | Gigavac 200 |  |  |  | 1
 |  | K2 | Gigavac 200 | Gigavac 200 |  |  |  | 1
G2RL-24_DC12 | RELAY GEN PURPOSE DPDT 8A 12V | K3, K4, K5 | G2RL | G2RL-24_DC12 |  | G2RL-24 DC12 |  | 3
LED GREEN 0603 |  | LED1, LED2, LED4, LED9, LED10 | LED 0603 GREEN | LED GREEN 0603 |  | LTST-C190KGKT |  | 5
LED RED 0603 | Red 631nm LED Indication - Discrete 2V 0603 (1608 Metric) | LED3 | LED 0603 RED | LED RED 0603 |  | LTST-C190KRKT |  | 1
DE4SRD | LED Bars and Arrays Red 640nm 300mcd Diffused Light Bar | LED6, LED8 | DE4SRD | DE4SRD |  |  | DE4SRD | 2
4-40 Mount Hole |  | MH1, MH2, MH3, MH4 | MH | 4-40 Mount Hole |  |  |  | 4
43045-0800 | CONN HEADER R/A 8POS 3MM | P1 | 430450800 | 43045-0800 |  |  | 43045-0800 | 1
43045-0200 | CONN HEADER R/A 2POS | P2, P7 | 430450200 | 43045-0200 |  |  | 43045-0200 | 2
43045-0400 | Male connector dual row 90° 3 mm Pole no. 2x2 Micro-Fit, 43045-0400, Molex | P8, P9 | 430450400 | 43045-0400 |  |  | 43045-0400 | 2
Screw Terminal 2x1 | Screw Terminal, 2-Pin | P10, P11 | 2POS TERM BLOCK | Screw Terminal 2x1 |  |  |  | 2
10k | RES SMD 10K OHM 5% 1/2W 0805 | R1, R3 | SMD-0805-RES | ERJ-P06J103V | P10KADCT-ND |  |  | 2
2.61k | RES SMD 2.61K OHM 1% 1/4W 1206 | R2, R4 | SMD-1206-RES | ERJ-8ENF2611V | P2.61KFCT-ND |  |  | 2
1k | RES SMD 1K OHM 1% 1/8W 0805 | R5, R6, R8, R9, R10, R12, R14, R15, R18 | SMD-0805-RES | ERJ-6ENF1001V | P1.00KCCT-ND |  |  | 9
1 | RES SMD 1 OHM 5% 1/3W 0805 | R7 | SMD-0805-RES | ERJ-6BQJ1R0V | P17527CT-ND |  |  | 1
LTO150F10000JTE3 | RES 1K OHM 5% 150W TO247-2 | R16, R17 | TO-247-2 | LTO150F10000JTE3 |  |  | LTO150F10000JTE3 | 2
DCM290P138T600A40 | DC DC CONVERTER 13.8V 600W | U1 | DCM290y138x600A40 | DCM290P138T600A40 |  | DCM290P138T600A40 |  | 1

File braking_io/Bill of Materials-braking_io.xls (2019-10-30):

Comment | Description | Designator | Footprint | LibRef | Quantity | Manufacturer P/N | DNP | Notes
PCR1J101MCL1GS | CAP ALUM POLY 100UF 20% 63V SMD | C1, C70, C71, C90 | CAPAE110103X126M | PCR1J101MCL1GS | 4 | 493-13783-1-ND
0.10µF | CAP CER 0.1UF 10V U2J 0805, CAP CER 0.1UF 16V X7R 0805, CAP CER 0.1UF 25V X7R 0805, CAP CER 0.1UF 50V X7R 0805 | C2, C3, C4, C9, C15, C16, C17, C18, C19, C20, C21, C22, C25, C26, C27, C28, C31, C32, C33, C34, C39, C40, C41, C42, C45, C46, C47, C48, C49, C50, C51, C52, C53, C54, C56, C58, C60, C62, C64, C66, C67, C68, C69, C73, C74, C75, C76, C84, C92, C93, C94 | SMD-0805C | GRM21B7U1A104JA01L, GRM219R71C104KA01D, GRM219R71E104KA01D, GCD21BR71H104KA01L, GRM219R71C104JA01D | 51 | 490-11592-1-ND
10000pF | CAP CER 10000PF 250V X7T 0805 | C5, C80 | SMD-0805C | GC321AD72E103KX01D | 2 | 490-13986-1-ND
22µF | CAP CER 22UF 25V X5R 1206 | C6, C10, C11, C12, C13, C14, C81, C85, C86, C87, C88, C89, C98, C99 | SMD-1206C | GRT31CR61E226ME01L, GRM31CR61E226KE15L | 14 | 490-12451-1-ND
4.7µF | CAP CER 4.7UF 50V X7S 1206 | C7, C8, C82, C83, C107 | SMD-1206C | GCM31CC71H475KA03L | 5 | 490-11167-1-ND
0.22µF | CAP CER 0.22UF 10V X7R 0805 | C23, C24, C29, C30, C35, C36, C43, C44 | SMD-0805C | LLA215R71A224MA14L | 8 | 490-4432-1-ND
4.7µF | CAP CER 4.7UF 6.3V X5R 0805 | C38 | SMD-0805C | GRM21BR60J475KA11L | 1 | 490-9749-1-ND
1µF | CAP CER 1UF 50V X7R 0805 | C55, C57, C59, C61, C63, C65, C72, C77, C78, C79, C97 | SMD-0805C | GRM21BR71H105KA12L, GCJ21BR71H105KA01L | 11 | 490-4736-1-ND
0.068µF | CAP CER 0.068UF 50V X7R 0805 | C95, C96 | SMD-0805C | GCJ21BR71H683KA01L | 2 | 490-5807-1-ND
10µF | CAP CER 10UF 50V X5R 1206 | C101, C102, C105 | SMD-1206C | GRM31CR61H106KA12L | 3 | 490-5961-1-ND
1µF | CAP CER 1UF 50V X7R 1206 | C103 | SMD-1206C | GCJ31MR71H105KA12L | 1 | 490-5810-1-ND
0.015µF | CAP CER 0.015UF 250V X7T 0805 | C104 | SMD-0805C | GC321AD72E153KX01D | 1 | 490-13987-1-ND
10pF | CAP CER 10PF 100V NP0 0805 | C106 | SMD-0805C | GQM2195C2A100GB01D | 1 | 490-6098-1-ND
B340A-13-F | DIODE SCHOTTKY 40V 3A SMA | D1, D18 | DIOM4326X20N | B340A-13-F | 2 | B340A-FDICT-ND
1N4148WQ-7-F | Diodes - General Purpose, Power, Switching SMT Fast Switching Diode | D2, D3, D4, D5, D6, D7, D8, D9 | INDM3838X18N | 1N4148WQ-7-F | 8 | 1N4148WQ-7-F
SMBJ15A | TVS DIODE 15V 24.4V DO214AA | D10, D11, D12, D13, D14, D15, D16, D17 | DIOM4436X26N | SMBJ15A | 8 | SMBJ15ALFCT-ND
CB61F15A-TR1 |  | F1, F2 | RESC6132X26N | CB61F15A-TR1 | 2 | 283-4104-1-ND
0410CDMCCDS-R10MC |  | L1 | INDM4442X20N | 0410CDMCCDS-R10MC | 1 | 308-2523-1-ND
IHLP3232DZER1R0M11 | Fixed Inductors 1uH 20% Low Profile | L2 | INDM8682X40N | IHLP3232DZER1R0M11 | 1 | 541-1348-1-ND
SRR1280A-330M | Inductor Power Shielded Wirewound 33uH 20% 1KHz 28Q-Factor Ferrite 3.5A 57mOhm DCR Automotive T/R | L3 | INDM120125X75N | SRR1280A-330M | 1 | 06X7909
SRR1210-390M | FIXED IND 39UH 4.2A 66 MOHM SMD | L4 | INDM120120X100N | SRR1210-390M | 1 | SRR1210-390MCT-ND
744066150 | FIXED IND 15UH 3.2A 50 MOHM SMD | L5 | INDP100100X38N | 744066150 | 1 | 732-1077-1-ND
GREEN |  | LED2, LED3, LED4, LED5, LED6, LED7, LED8, LED9 | LED 0603 GREEN | LED GREEN 0603 | 8 | LTST-C190KGKT
LED GREEN 0603 |  | LED, LED1, LED10, LED11 | LED 0603 GREEN | LED GREEN 0603 | 4 | LTST-C190KGKT
4-40 Mount Hole |  | MH1, MH2, MH3, MH4 | MH | 4-40 Mount Hole | 4 |  | DNP
43045-1000 | GLOVE, POLYAMIDE, L/FREE, PU, SIZE 6 - More Details | P1, P8, P9 | 430451000 | 43045-1000 | 3 | 43045-1000
43045-0800 | CONN HEADER R/A 8POS 3MM | P2, P10, P15 | 430450800 | 43045-0800 | 3 | 43045-0800
Header 2 | Header, 2-Pin | P3, P4, P5, P6, P11, P13, P14 | Pin Header 1x2 TH Pitch 2.54mm | Header 2 | 7
43045-2400 | Molex MICRO-FIT 3.0 Series, Series Number 43045, 3mm Pitch 24 Way 2 Row Right Angle PCB Header, Solder Termination, 5A | P7 | 430452400 | 43045-2400 | 1 | 43045-2400
Header 3 | Header, 3-Pin | P12 | Pin Header 1x3 TH Pitch 2.54mm | Header 3 | 1
43045-0200 | CONN HEADER R/A 2POS | P16 | 430450200 | 43045-0200 | 1 | 43045-0200
MMBT3906 |  | Q1, Q2, Q3, Q4, Q5, Q6, Q7, Q8 | SOTFL103P240X110-3N | MMBT3906-7-F | 8 | MMBT3906-FDICT-ND
0.18 | RES SMD 0.18 OHM 1% 1/2W 1206 | R1 | SMD-1206-RES | ERJ-8BSFR18V | 1 | P17683CT-ND
0.002 | RES SMD 0.002 OHM 1% 1W 1206 | R2 | SMD-1206-RES | ERJ-MP2MF2M0U | 1 | P19341CT-ND
16k | RES SMD 16K OHM 1% 1/8W 0805 | R3, R14 | SMD-0805-RES | ERJ-6ENF1602V | 2 | P16.0KCCT-ND
100k | RES SMD 100K OHM 5% 1/2W 0805 | R4, R21, R22, R23, R24, R29, R30, R31, R33, R37, R38, R39, R40, R55, R56, R57, R58 | SMD-0805-RES | ERJ-P06J104V | 17 | P100KADCT-ND
30k | RES SMD 30K OHM 1% 1/8W 0805 | R5, R13, R16, R73, R74, R75, R76, R93, R94, R95, R96, R105, R106, R152, R155 | SMD-0805-RES | ERJ-6ENF3002V | 15 | P30.0KCCT-ND
10k | RES SMD 10K OHM 5% 1/2W 0805, RES SMD 10K OHM 1% 1/2W 0805 | R6, R7, R10, R15, R17, R18, R19, R20, R27, R28, R35, R36, R53, R54, R103, R104, R107, R108, R109, R110, R111, R114, R115, R116, R117, R118, R119, R120, R123, R124, R129, R130, R133, R134, R135, R136, R143, R144, R145, R146, R149, R154, R156, R157, R163, R166 | SMD-0805-RES | ERJ-P06J103V, ERJ-P06F1002V | 46 | P10KADCT-ND, P16059CT-ND | [NoParam], DNP, [NoValue]
10k | RES SMD 10K OHM 5% 1/2W 0805, RES SMD 10K OHM 1% 1/2W 0805 | R6, R7, R10, R15, R17, R18, R19, R20, R27, R28, R35, R36, R53, R54, R103, R104, R107, R108, R109, R110, R111, R114, R115, R116, R117, R118, R119, R120, R123, R124, R129, R130, R133, R134, R135, R136, R143, R144, R145, R146, R149, R154, R156, R157, R163, R166 | SMD-0805-RES | ERJ-P06J103V, ERJ-P06F1002V | 46 | P10KADCT-ND, P16059CT-ND | [NoParam], DNP, [NoValue]
0.01 | RES SMD 0.01 OHM 1% 1/2W 1206 | R8, R147 | SMD-1206-RES | ERJ-MP2KF10MU | 2 | P19322CT-ND
1k | RES SMD 1K OHM 5% 1/2W 0805 | R9, R148, R162, R165 | SMD-0805-RES | ERJ-P06J102V | 4 | P1.0KADCT-ND
330 | RES SMD 330 OHM 5% 1/2W 0805 | R11, R150 | SMD-0805-RES | ERJ-P06J331V | 2 | P330ADCT-ND
3.24k | RES SMD 3.24K OHM 1% 1/8W 0805 | R12 | SMD-0805-RES | ERJ-6ENF3241V | 1 | P3.24KCCT-ND
200 | RES SMD 200 OHM 1% 1/2W 0805, RES SMD 200 OHM 1% 1/8W 0805 | R25, R26, R32, R34, R41, R42, R59, R60, R77, R78, R79, R80, R97, R98, R99, R100, R164, R167 | SMD-0805-RES | ERJ-P06F2000V, ERJ-6ENF2000V | 18 | P16064CT-ND, P200CCT-ND
0 | RES SMD 0.0 OHM JUMPER 1/8W 0805 | R43, R44, R45, R46, R47, R48, R49, R50, R51, R52, R61, R62, R63, R64, R65, R66, R67, R68, R69, R70, R71, R72, R81, R82, R83, R84, R85, R86, R87, R88, R89, R90, R91, R92, R101, R102, R112, R113, R121, R122, R125, R126, R127, R128, R131, R137, R138, R139, R140, R141 | SMD-0805-RES | ERJ-6GEY0R00V | 50 | P0.0ACT-ND | DNP, [NoParam]
0 | RES SMD 0.0 OHM JUMPER 1/8W 0805 | R43, R44, R45, R46, R47, R48, R49, R50, R51, R52, R61, R62, R63, R64, R65, R66, R67, R68, R69, R70, R71, R72, R81, R82, R83, R84, R85, R86, R87, R88, R89, R90, R91, R92, R101, R102, R112, R113, R121, R122, R125, R126, R127, R128, R131, R137, R138, R139, R140, R141 | SMD-0805-RES | ERJ-6GEY0R00V | 50 | P0.0ACT-ND | DNP, [NoParam]
1.8k | RES SMD 1.8K OHM 1% 1/2W 0805 | R151 | SMD-0805-RES | ERJ-P6WF1801V | 1 | P16888CT-ND
12k | RES SMD 12K OHM 1% 1/2W 0805 | R153 | SMD-0805-RES | ERJ-P6WF1202V | 1 | P16898CT-ND
2M | RES SMD 2M OHM 1% 1/8W 0805 | R158 | SMD-0805-RES | ERJ-6ENF2004V | 1 | P2.00MCCT-ND
49.9k | RES SMD 49.9K OHM 1% 1/8W 0805 | R159 | SMD-0805-RES | ERJ-6ENF4992V | 1 | P49.9KCCT-ND
34.8k | RES SMD 34.8K OHM 1% 1/8W 0805 | R160 | SMD-0805-RES | ERJ-6ENF3482V | 1 | P34.8KCCT-ND
86.6k | RES SMD 86.6K OHM 1% 1/8W 0805 | R161 | SMD-0805-RES | ERJ-6ENF8662V | 1 | P86.6KCCT-ND
NCP21XM472J03RA | NTC THERMISTOR 4.7K OHM 5% 0805 | TH1, TH2 | SMD-0805-RES | NCP21XM472J03RA | 2 | NCP21XM472J03RA | DNP
TP | SMD TEST POINT | TP1, TP2, TP9, TP10, TP11, TP12, TP13, TP14, TP15, TP16, TP17, TP18, TP19, TP20, TP21, TP22, TP23, TP24, TP25, TP26, TP27, TP28, TP29, TP30, TP31, TP32, TP33, TP34, TP35, TP36, TP37, TP38, TP39, TP40, TP41, TP42, TP43, TP44, TP45, TP46, TP47, TP48, TP49, TP50, TP51, TP52, TP53, TP54, TP55, TP56, TP57, TP60, TP61, TP62, TP63, TP64, TP65, TP66, TP67, TP68, TP69, TP70, TP71, TP72, TP73, TP74, TP75, TP76, TP79, TP80, TP81, TP82, TP83, TP84, TP86, TP87, TP88, TP89, TP90, TP91, TP92, TP93 | Test Point | TP | 82 |  | DNP
2mm_Fiducial |  | TP5, TP6, TP7, TP8 | 2mm_Fiducial | 2mm_Fiducial | 4 |  | DNP
INA240x | IC AMP CURRENT SENSE 8-TSSOP | U1, U4, U25 | SOIC127P600X175-8N | INA240x | 3 | INA240A1PWR
TL071CDR | IC OPAMP JFET 3MHZ 8SOIC | U2, U5 | SOP127P600X175-8N | TL071CDR | 2 | 296-14994-1-ND
TPS5420 |  | U3, U24 | SOP127P600X175-8N | TPS5420 | 2 | 296-19671-5-ND
MPQ6610 |  | U6, U7, U8, U9, U10, U11, U14, U15 | SOP127P600X175-8N | MPQ6610 | 8 |  |  | Provided by MPS
MCP23017T-E/SO | IC I/O EXPANDER I2C 16B 28SOIC | U12 | SOIC28-W_MC-M | MCP23017T-E/SO | 1 | MCP23017T-E/SO
TPC817 | OPTOISO 5KV TRANS 4SOP | U13, U27 | SOT200P1005X328-5N | TPC817 | 2 | TPC817S1B RAG
REF194GSZ | IC VREF SERIES 4.5V 8SOIC | U16, U18 | SOP127P600X175-8N | REF194GSZ | 2 | REF194GSZ-ND
ADC128D818CIMTX/NOPB | Analog to Digital Converters - ADC | U17, U19 | TSOP65P660X120-16N | ADC128D818CIMTX/NOPB | 2 | 296-41182-1-ND
SLG46826 | GreenPAK Programmable Mixed Signal Matrix with In-System Programmability | U20 | SOP65P640X175-20N | SLG46826 | 1 | 03AH3078
MAX3232CDR | IC DRVR/RCVR MULTCH RS232 16SOIC | U21 | SOP127P1060X175-16N | MAX3232CDR | 1 | 296-13094-1-ND
NUCLEO-L432KC | BOARD NUCLEO STM32F303K8T6 | U22 | NUCLEO-L432KC | NUCLEO-L432KC | 1 | 497-15981-ND
CAT24C32WIGT3 | IC EEPROM 32K I2C 1MHZ 8SOIC | U23 | SOP127P600X175-8N | CAT24C32WIGT3 | 1 | 06R0561
LTC3114-1 |  | U26 | TSOP65P640X110_HS-17N | LTC3114-1 | 1 | LTC3114EFE-1#TRPBFCT-ND

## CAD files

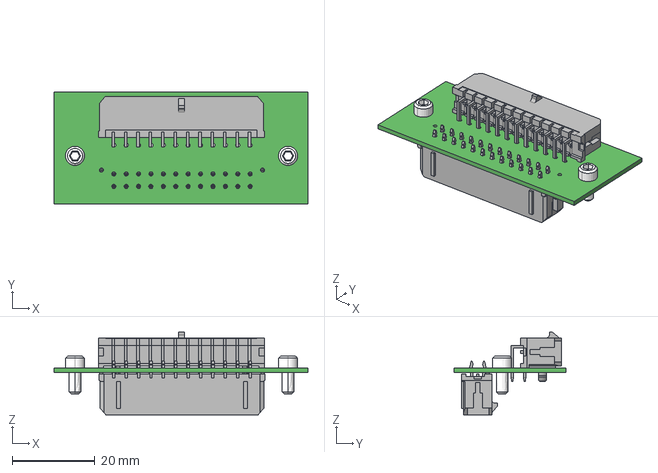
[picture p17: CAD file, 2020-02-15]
breakout_board/breakout_board.step
61.5 x 27.2 x 20.1 mm

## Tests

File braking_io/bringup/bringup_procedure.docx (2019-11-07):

Braking IO Rev A Bring Up Procedure

11/6/2019

Purpose

This document is designed to list the steps required to bring up the Rev A Braking IO PCBs.

Initial Inspection and Continuity Checks

1. Check packaging for any visible damage from shipping.
2. Open package and verify 5 bare PCBs arrived
3. Inspect the board for any visual defects, including poor soldermask, damaged pads, etc.
4. Check power rails
  a. On each IC, verify VCC and GND are present on the appropriate pad
  b. Verify power rails are not shorted together
  c. Verify power rails are not shorted to GND
    i. V-BUS
    ii. V-POS7V
    iii. V-POS5V
    iv. V-POS3V3
5. Check for undrilled vias and through holes
6. Check for any shorted pads or traces

Solder Paste

1. Ensure you have a fresh, refrigerated tube of solder paste
2. If desired, laser cut a sheet of mylar
3. Apply solder paste to each pad
  a. Avoid applying too much solder paste
  b. Avoid applying too little solder paste

Organizing Components

1. Organizing components beforehand can be a huge timesaver when doing assembly by hand. I recommend splitting your components into groups (resistors, capacitors, ICs, etc and arrange them in alpha-numeric order.
  a. This set of components was a self-contained digikey order, so if should be easier to find what you need.
2. Print off a copy of a BOM (and Schematics if desired)
3. Make sure you check the schematic for DNP components, If a component is DNP, that means DO NOT POPULATE! This could be done for a number of reasons like configuration options, addressing, or flexibility.

Place SMD Components

1. It is recommended to place the power supply components first and verify the supplies are functional before placing the rest of your components. Remember, boards are cheap, components are expensive.
2. Reflow components using an oven (preferred) or a hot air tool, reflow your components
  a. Inspect the board after to make sure all solder joints were reflowed
  b. Inspect the board after to make sure there are no shorts
  c. If necessary, populate a 24V header so you can power on the initial supplies
3. Performing continuity checks, especially on your power rails and when everything is as expected, power on the board and verify all of the power rails are coming up appropriately
  a. Be sure to set the power supply to 24V and 500mA current limit
4. Fill in the table after powering on the board

Rail | Expected | Actual
V-BUS | 24V (Power supply)
V-POS7V | 7V +/- 2%
V-POS5V | 5V +/- 2%
V-POS24V | 24V +/- 1%
V-POS3V3 (After Nucleo populated) | 3.3V +/- 2%

5. After power supplies are placed and verified, place the rest of the SMD components
  a. Note, only place one of the solenoid driver circuits and verify that circuit is working before placing the rest of the ICs
6. Reflow components, as before
7. Inspect and touch up any open circuits or shorts

Place Through Hole Components

1. Almost there! Solder your through hole components to the board
2. Perform one last continuity check on the power rails

Power on the Board!

1. Set a current limit on the supply.
2. Connect the board to power
3. Be prepared to power off the supply in the event of a short circuit (indicated by either hitting the current limit or magic smoke coming off of the board)

Verify Sub-Circuits

Some circuits can be tested more easily than others. Below is a recommended test procedure

Tests that can be performed without software support:

1. Voltage telemetry on all rails (Measure the output of the Op-Amp and verify it corresponds to the actual measurement)

Rail | Expected Range | Measured Value
V-BUS | 1.82V-2.54V
V-POS7V | 4.1V-4.2V
V-POS5V | 3.9V-4.0V
V-POS24V | No Telem

2. Current Telemetry on all rails (Measure on the output of the INA240x)

Rail | Expected Range | Measured Value
V-BUS | 4.0V Max
V-POS7V | 4.0V Max
V-POS5V | 4.0V Max
V-POS24V | No Telem

3. Verify Pressure Sensor Circuit
  a. This is a lower priority circuit to test, as it’s a direct copy from Pod IV
  b. Connect a pressure sensor to P12 and verify the output is appropriate.
  c. Bonus: Connect to a pressurized system

Sensor Number | Sensor Type | Expected Vout | Measured Vout

4. Verify Temperature circuit
  a. Similar to the pressure sensor circuit, verify the output voltage is appropriate for the thermistor.
  b. Verify the voltage changes with temperature

Expected Vout @ Room Temp | Measured Vout @ Room Temp | Expected Vout @ 40C | Measured Vout @ 40C

5. Verify Retroreflective Circuit
  a. Connect a retroreflective sensor to the header
  b. Flash a retro tape and confirm:
    i. LED output changes
    ii. Voltage changes on the negative edge

Retro Number | Pass?
1
2

6. Verify Solenoid Driver Circuit
  a. Connect a solenoid to the solenoid header
  b. Drive the solenoid EN signal (Either manually, or via controls if they are ready)
  c. Ensure that the solenoid is driven
  d. Measure how power consumption

Solenoid Number | Actuates? | Unactuates? | Nominal Power Consumption | Max Power Consumption
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
7. Verify Watchdog Circuit
  a. Watchdog design must be completed first
8. Verify I2C Devices
  a. Relies heavily on controls
  b. I2C Scan can be implemented through MBED OS
9. Verify UART Circuit

Note: The STM32L432KC has a quick and dirty compiler called MBED OS that you can write quick programs to test hardware functionality of the microcontroller. Production code won’t necessarily use this, but verifying hardware is important. Remember, the goal of the document is to have the firmware engineers not able to blame all of the troubles on hardware issues! If you can verify with MBED, you can likely say “sounds like a firmware issue”

Debugging

Some general tips on circuit debugging:

1. Thou shall check voltages
  a. Seriously, 95% of issues for projects like this are either an unplugged power supply, disabled power supply
2. Thou shall understand what circuit you are trying to test
  a. Is it really borked? Or do I just not understand what’s actually going on? Re-read your datasheet, pull up the schematic
3. Thou shall check continuity
  a. Go around all of the pins for your IC and verify they are connected properly. In my experience, it could be a bad lead, bad solder connection, or even a misspelled net name on your schematic. Don’t fret, you can always bluewire low current connections you might be missing!
  b. Also make sure you have placed all of the components. Last year we were plagued by missing 0-ohm resistors or other configurations
4. Thou shall check voltages
  a. See 1

Congrats

If you’ve made it this far, you should have a completed, functional, non-buggy PCB!

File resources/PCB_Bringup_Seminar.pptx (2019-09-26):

## PCB Bring-up Seminar

2/14/2019 & 2/15/2019
Ryan Castle

## Objectives / Questions to Answer

- Developing Production Hardware
- Where do I find information to build a board?
- What Atlium tools do I need to know how to use?
- What materials do I need?
- Soldering 101
- Build up test PCBs

## End Goal

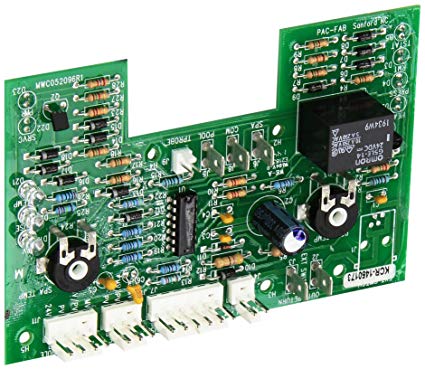
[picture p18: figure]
Image result for circuit board

- Functional Circuit Board capable of going into the pod
  - Populated PCBs
  - Soldering components is only ½ of the task
  - Bring-up instructions include basic testing information
- Be able to blame issues on the software and controls team

## Disclaimer

- We’ve spent a lot of time designing these PCBs and have spent ~$800 on components (~$2000 including sponsored components/PCBs)
- If you aren’t sure, ask
  - Definitely possible a mistake was made in schematic design or layout
- Practice on a test PCB
- Follow bring up instructions closely
- Inspect, inspect, inspect before you power on
  - No boards should be powered on for the first time without approval from Ethan or Ryan
  - Magic Smoke
- Mistakes are ok, we just want to avoid them
- Material might be really boring if you’ve done this before

## Altium Repository

- https://github.com/badgerloop-software/podiv-altium
- Primary source for all PCB information
- Possible to build a board from outputs
  - However, cloning the repo can speed up process
- Schematics, Layout files
  - Podiv-Altium/board_release/<pcb_name>/<revision_letter>/output/<*SCH*>
- Bringup Documentation
  - Podiv-Altium/bringup/<pcb_name>/<pcb_name>_bringup.docx

## Altium Tools

- Search for a Reference Designator (R1, U3, LED2)
  - In Schematics: <CTRL> + <F>
  - In Layout: <J>+<C>
- More information on a component
  - In Schematic:
    1. Double click on Component and the properties window will appear
    2. Click on the Properties Tab
    3. Manufacturer, P/N, Digikey P/N, link will appear.
    - Disclaimer: Sometimes, the parts to be populated won’t match with what’s in the schematic. This is because sometimes 2 components will have the same footprint or a BOM change was required for part availability

## Material Required

- See Bring-up Documentation
- Example for Ideal Diode PCB:
  - P4_LV_IdealDiode_001_REVA PCBs
  - Soldering iron
  - Solder
  - Solder Paste
  - Side cutters (snips)
  - PCB BOM
  - Oven

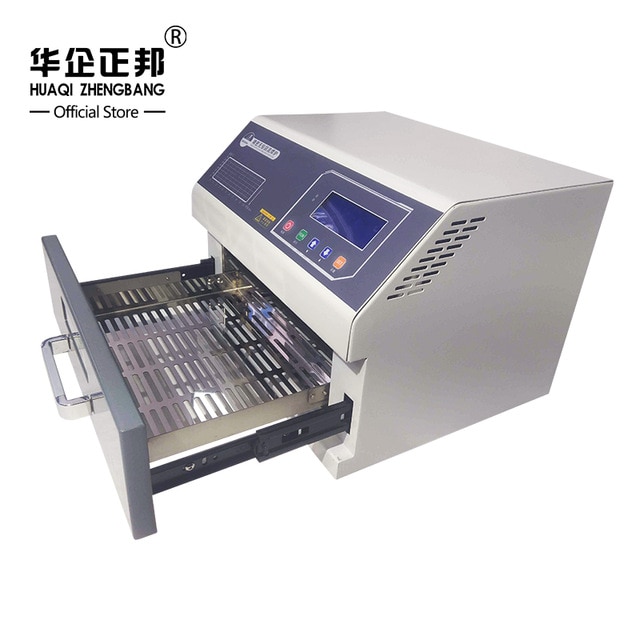
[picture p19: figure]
Image result for solder oven

## SMD Soldering

- https://mediaspace.wisc.edu/media/ECE370PowerSupplySM2-DVD/0_qaluf0im
  - Courtesy of Mark Allie, ECE 370
- Check Oven Settings
  - For this seminar, see if other groups are almost ready to use the oven. Possible to do multiple boards at once.

## What do I do if I find a problem with a board? Feature Request?

- Possible Answers:
A. Scream
B. Shout
C. Ignore it and hope it will go away
D. Submit a Feature Request or Bug Report on Github

Answer: All Except C
https://github.com/badgerloop-software/podiv-altium/issues

## Bring-up PCBs

- 2-3 people per PCB
- Boards:
  - Test PCBs (x2)
  - Processor (x5)
  - Ideal Diode (x2)
  - High Voltage Battery Breakout (x6) (Through Hole Only)
- Parts are all in the Digikey Box
  - Probably going to be a bottle neck. Be patient

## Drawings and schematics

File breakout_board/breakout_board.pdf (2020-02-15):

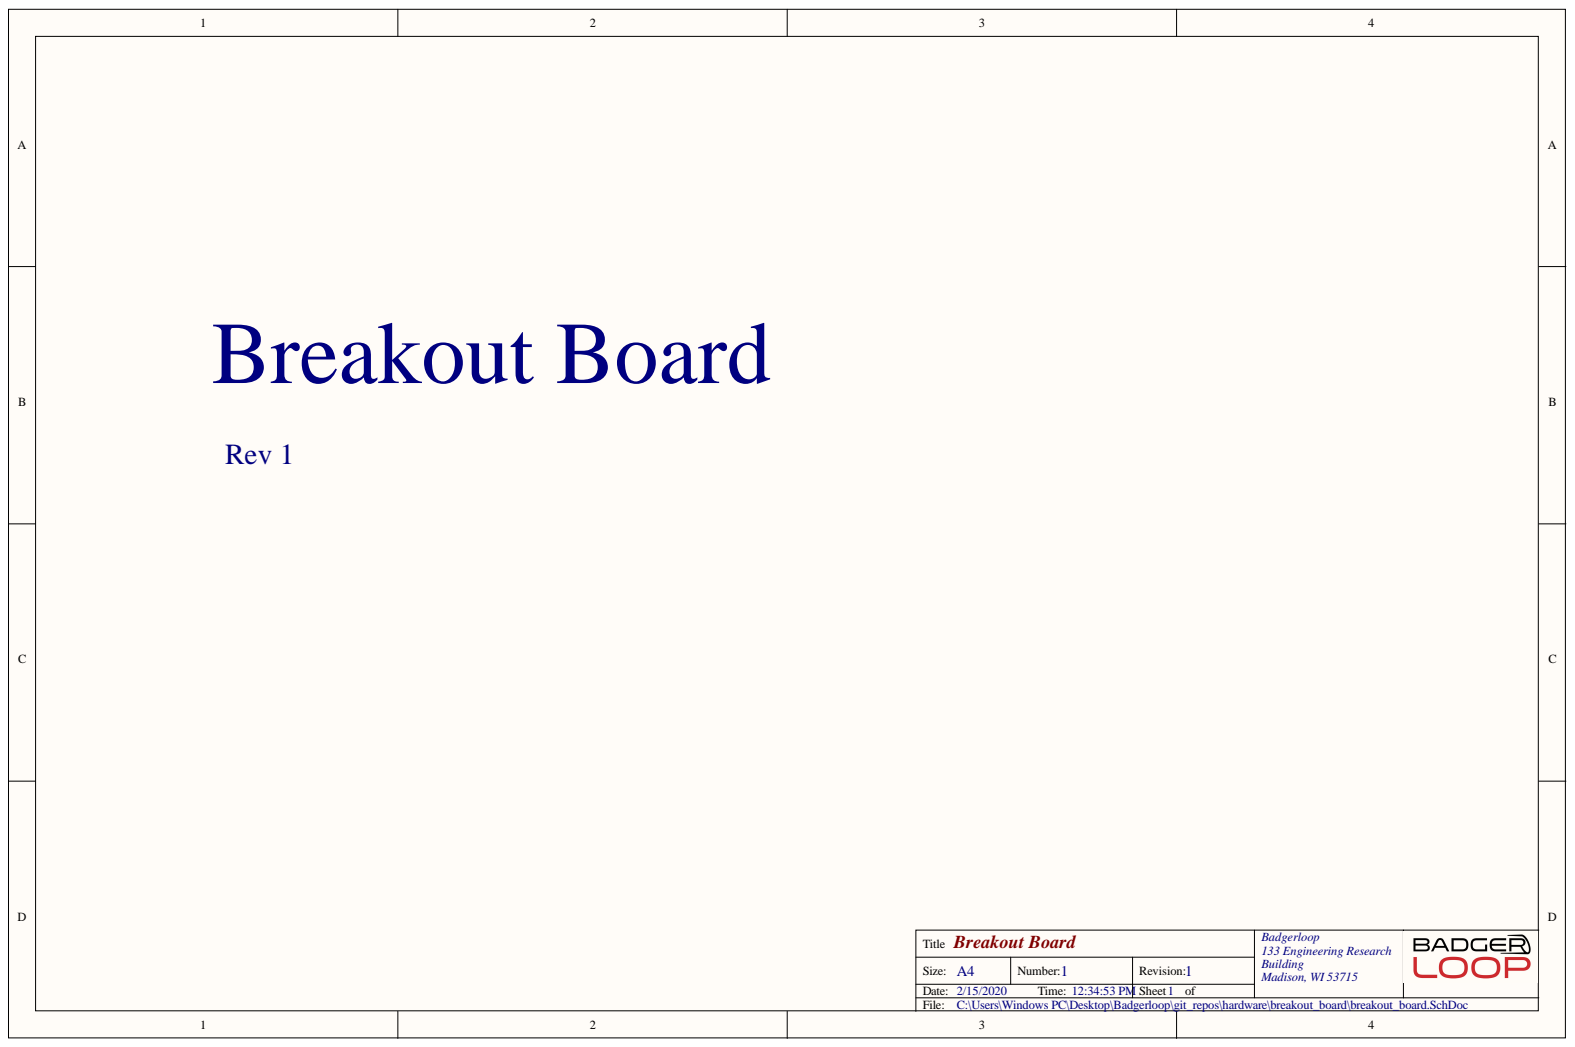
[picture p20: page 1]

Breakout Board Title | Badgerloop 133 Engineering Research Building Madison, WI 53715

A4 Size: | 1 Number: | 1 Revision:

Date: 2/15/2020 Time: 12:34:53 PM | | Sheet 1 of
File: C:\Users\Windows PC\Desktop\Badgerloop\git_repos\hardware\breakout_board\breakout_board.SchDoc

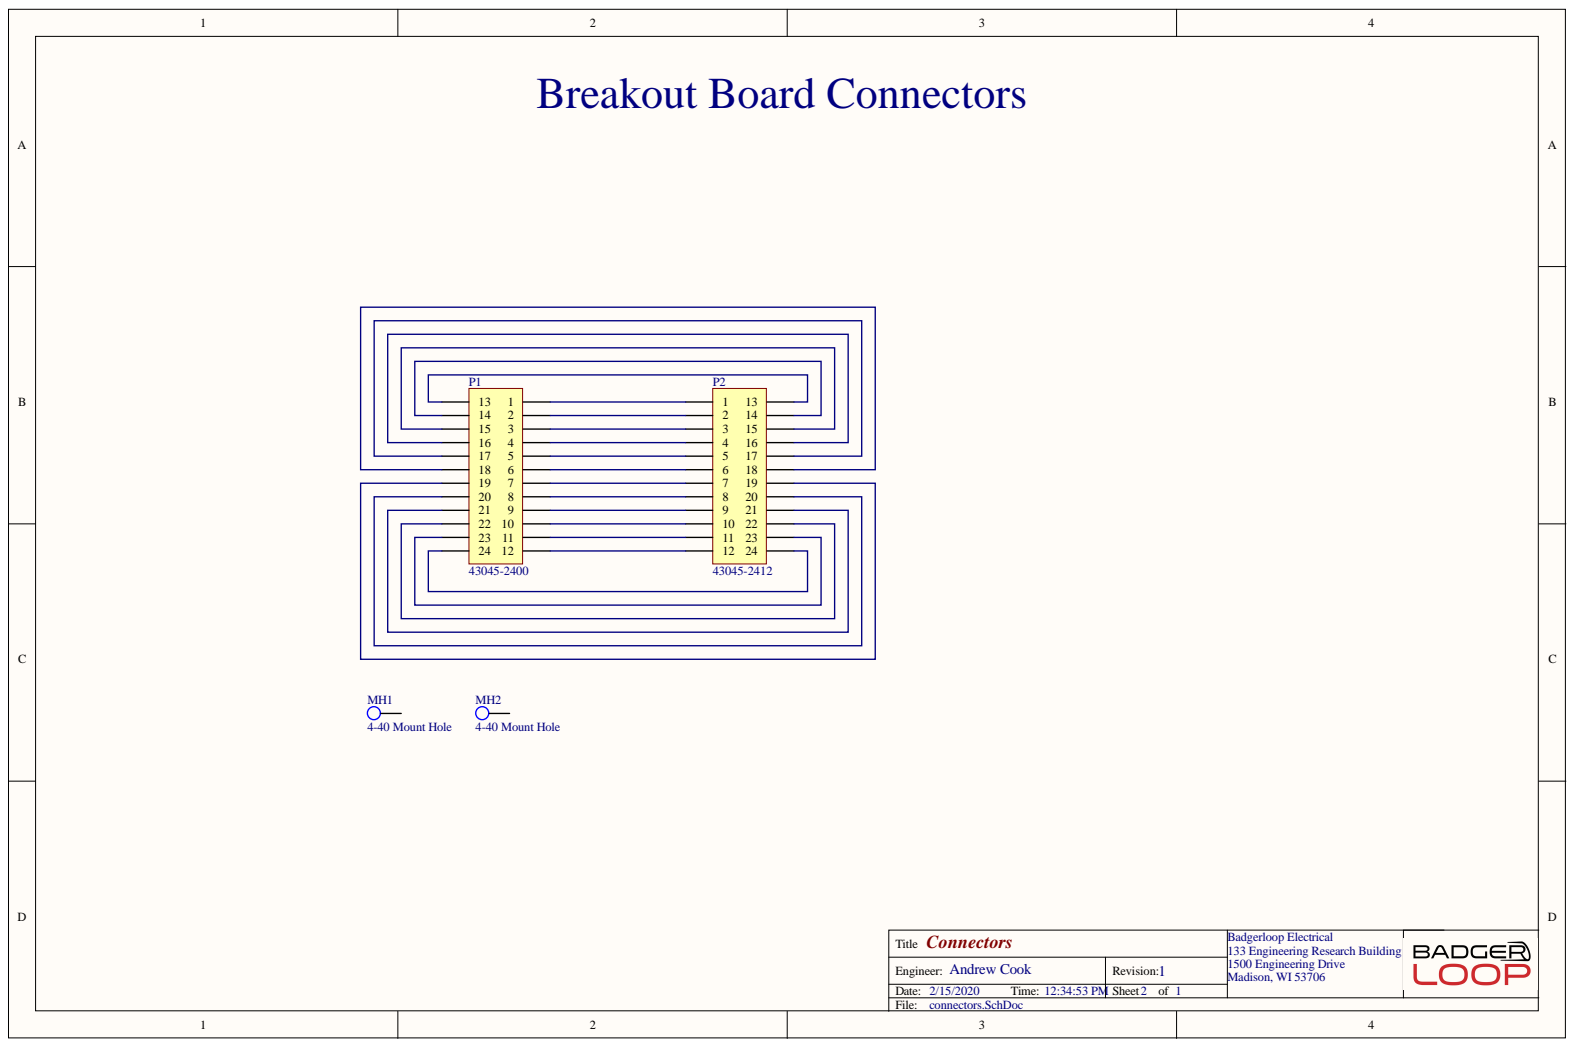
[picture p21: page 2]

Connectors Title | Badgerloop Electrical 133 Engineering Research Building 1500 Engineering Drive Madison, WI 53706

Andrew Cook Engineer: | 1 Revision:

Date: 2/15/2020 Time: 12:34:53 PM | Sheet 2 of 1
File: connectors.SchDoc

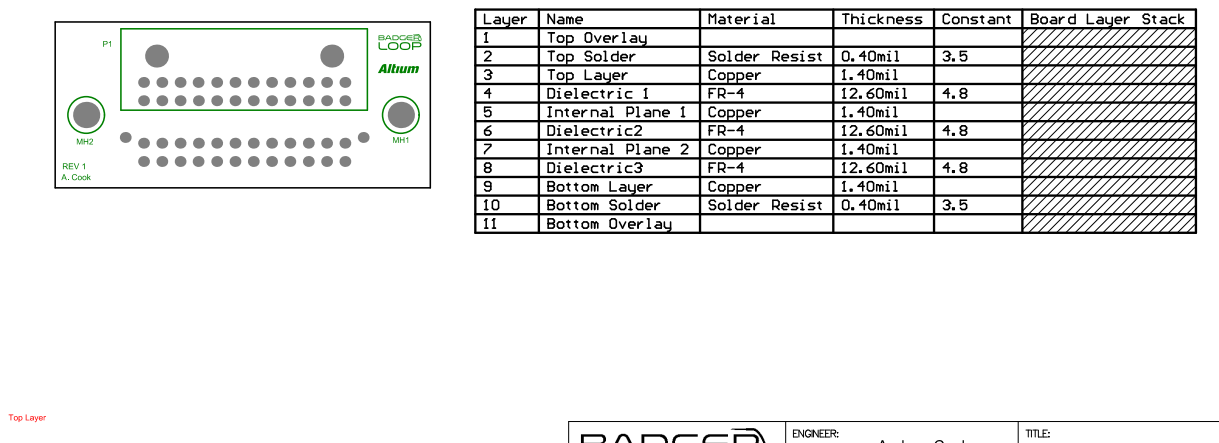
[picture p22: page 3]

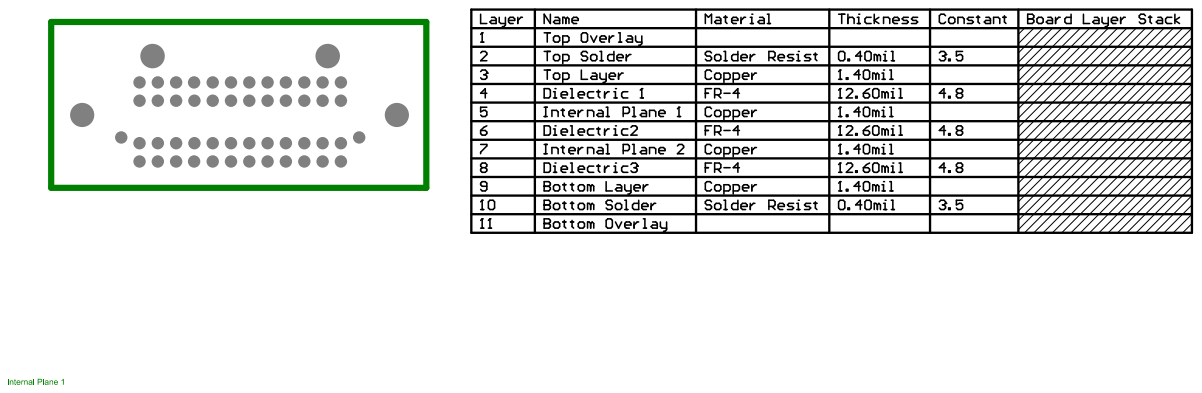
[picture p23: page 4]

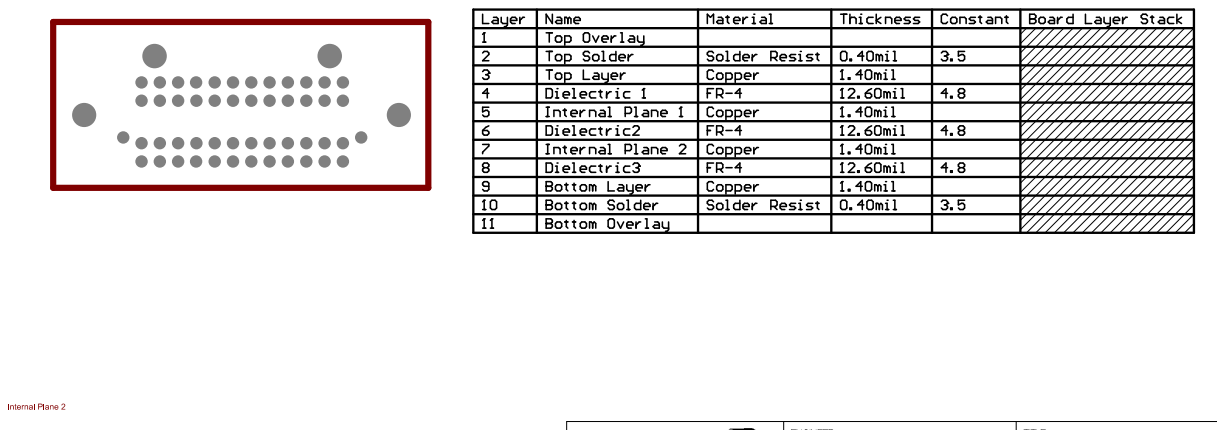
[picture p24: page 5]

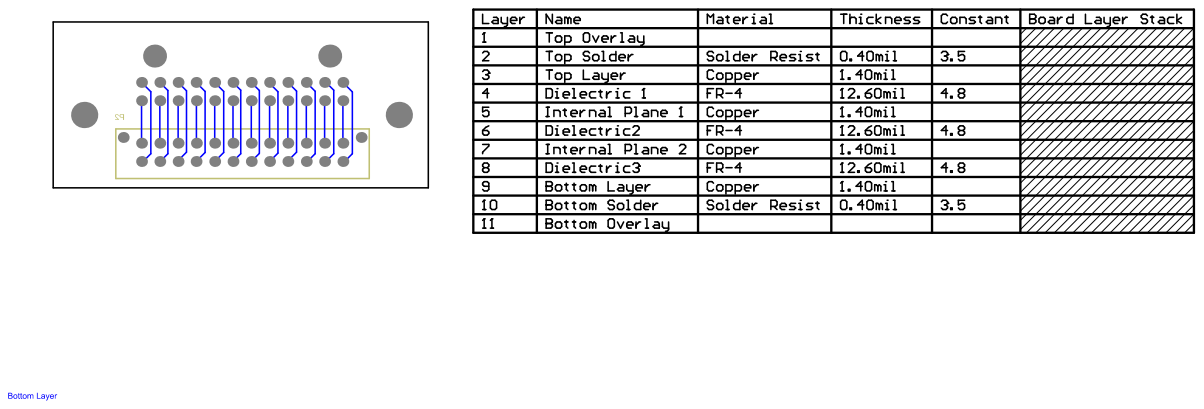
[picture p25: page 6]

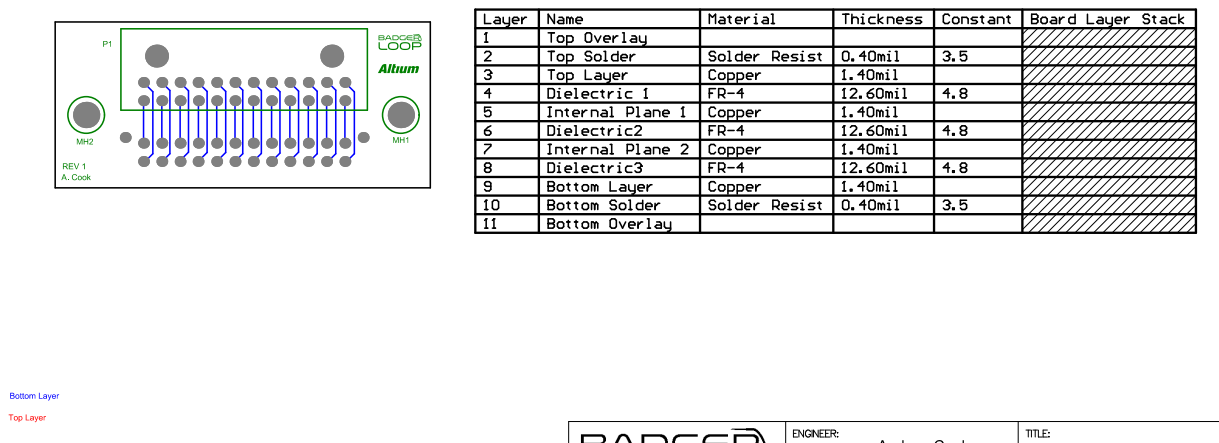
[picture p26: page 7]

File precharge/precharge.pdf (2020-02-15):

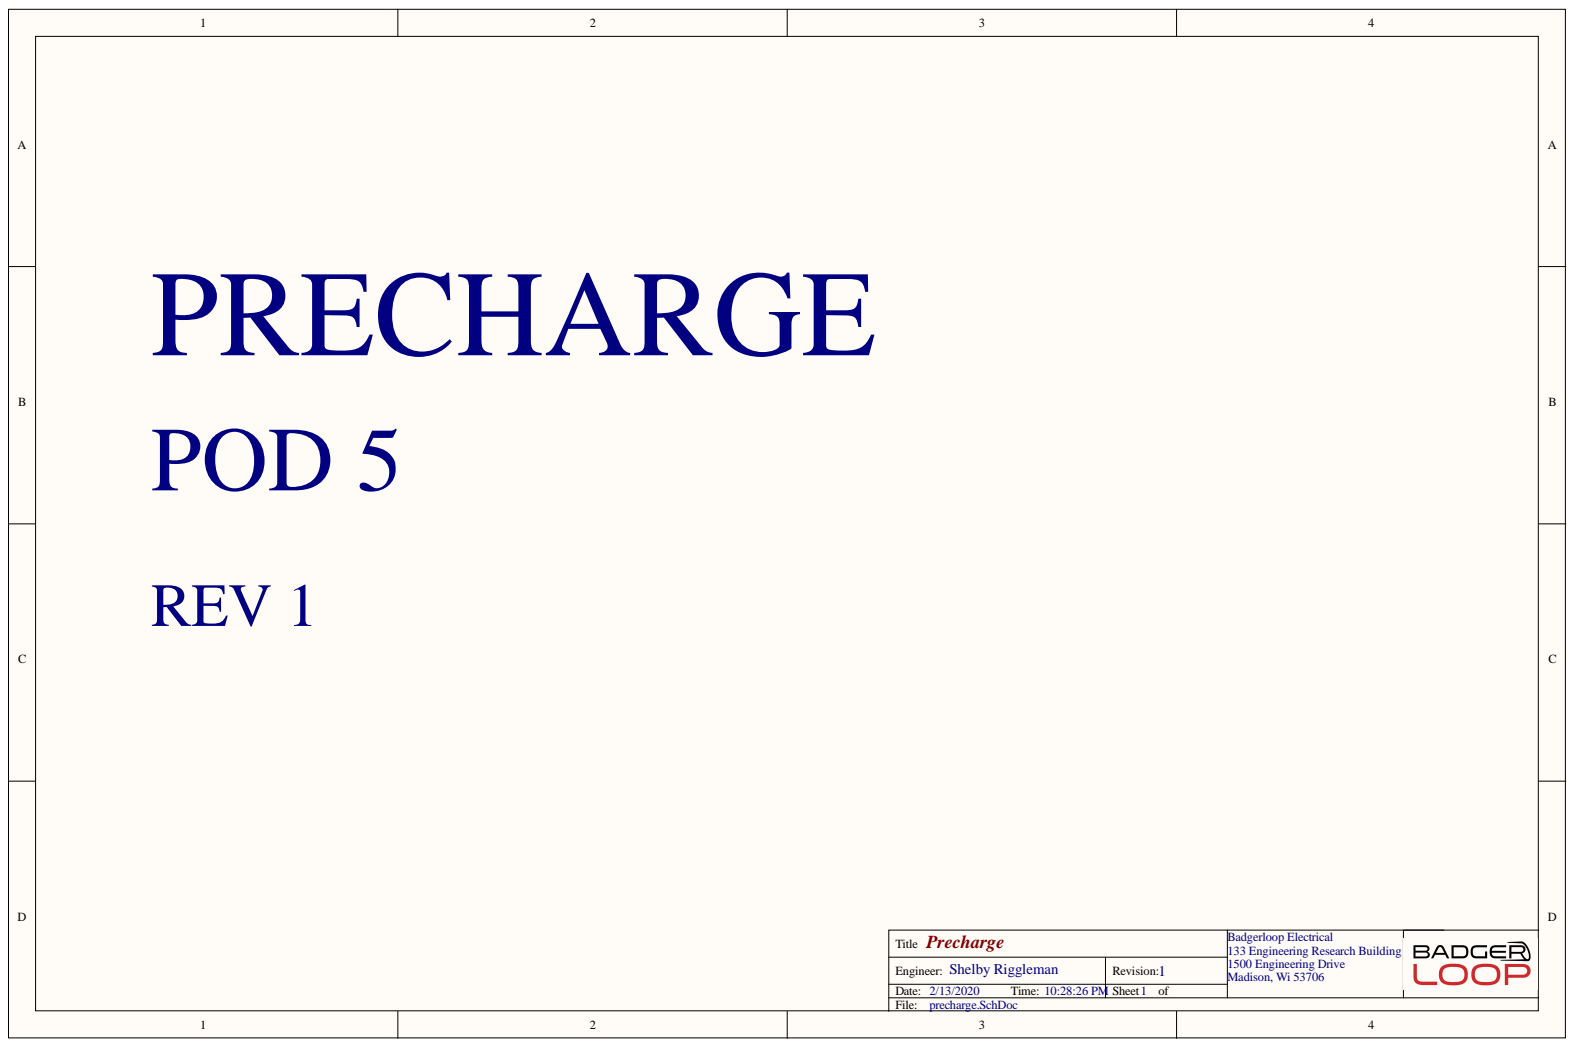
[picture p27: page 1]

Precharge Title | Badgerloop Electrical 133 Engineering Research Building 1500 Engineering Drive Madison, Wi 53706

Shelby Riggleman Engineer: | 1 Revision:

Date: 2/13/2020 Time: 10:28:26 PM | Sheet 1 of
File: precharge.SchDoc

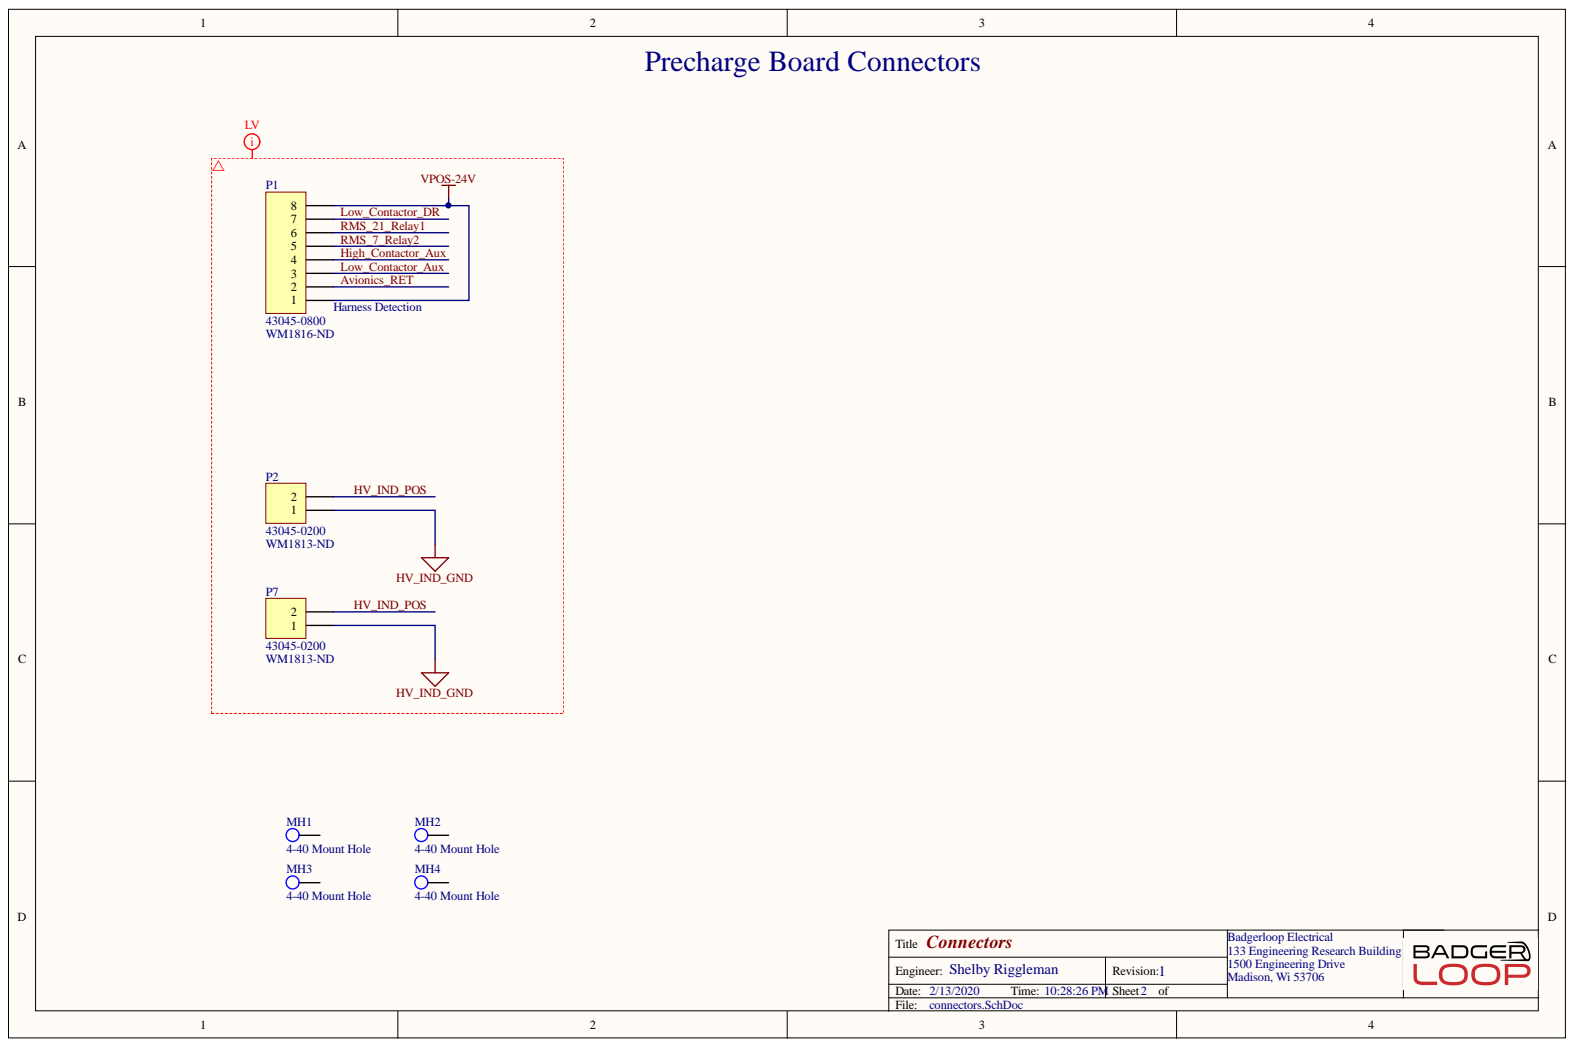
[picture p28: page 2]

Connectors Title | Badgerloop Electrical 133 Engineering Research Building 1500 Engineering Drive Madison, Wi 53706

Shelby Riggleman Engineer: | 1 Revision:

Date: 2/13/2020 Time: 10:28:26 PM | Sheet 2 of
File: connectors.SchDoc

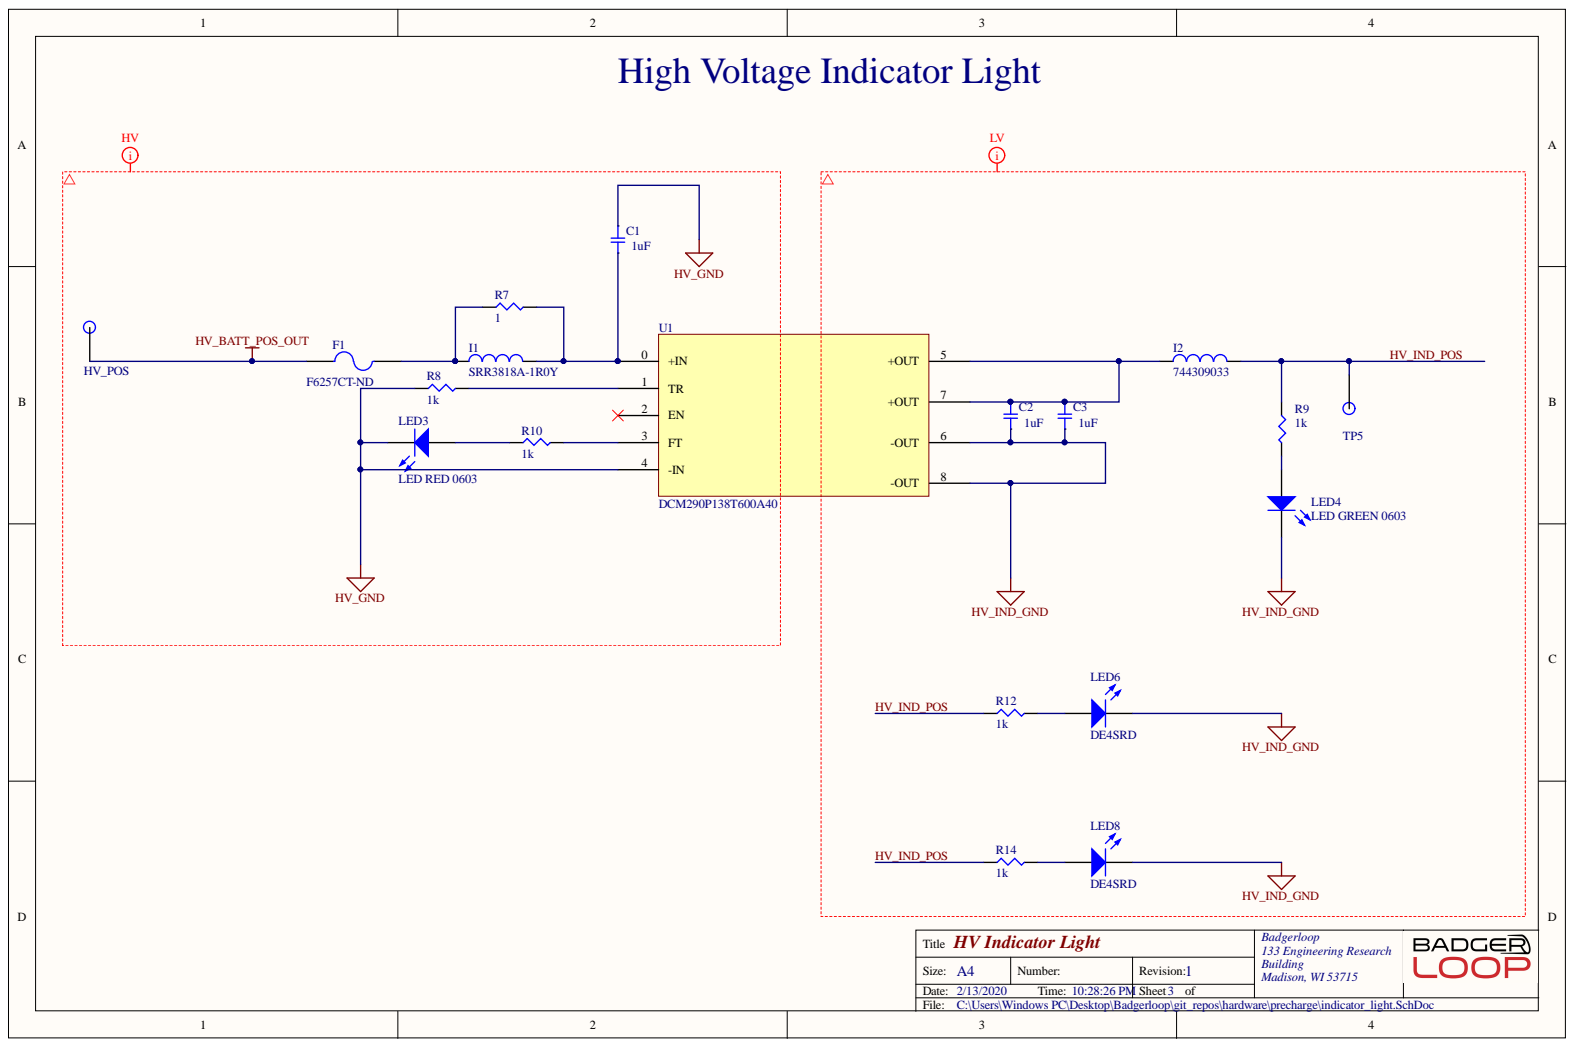
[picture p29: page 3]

High Voltage Indicator Light

HV Indicator Light Title | Badgerloop 133 Engineering Research Building Madison, WI 53715

A4 Size: | Number: | 1 Revision:

Date: 2/13/2020 Time: 10:28:26 PM | | Sheet 3 of
File: C:\Users\Windows PC\Desktop\Badgerloop\git_repos\hardware\precharge\indicator_light.SchDoc

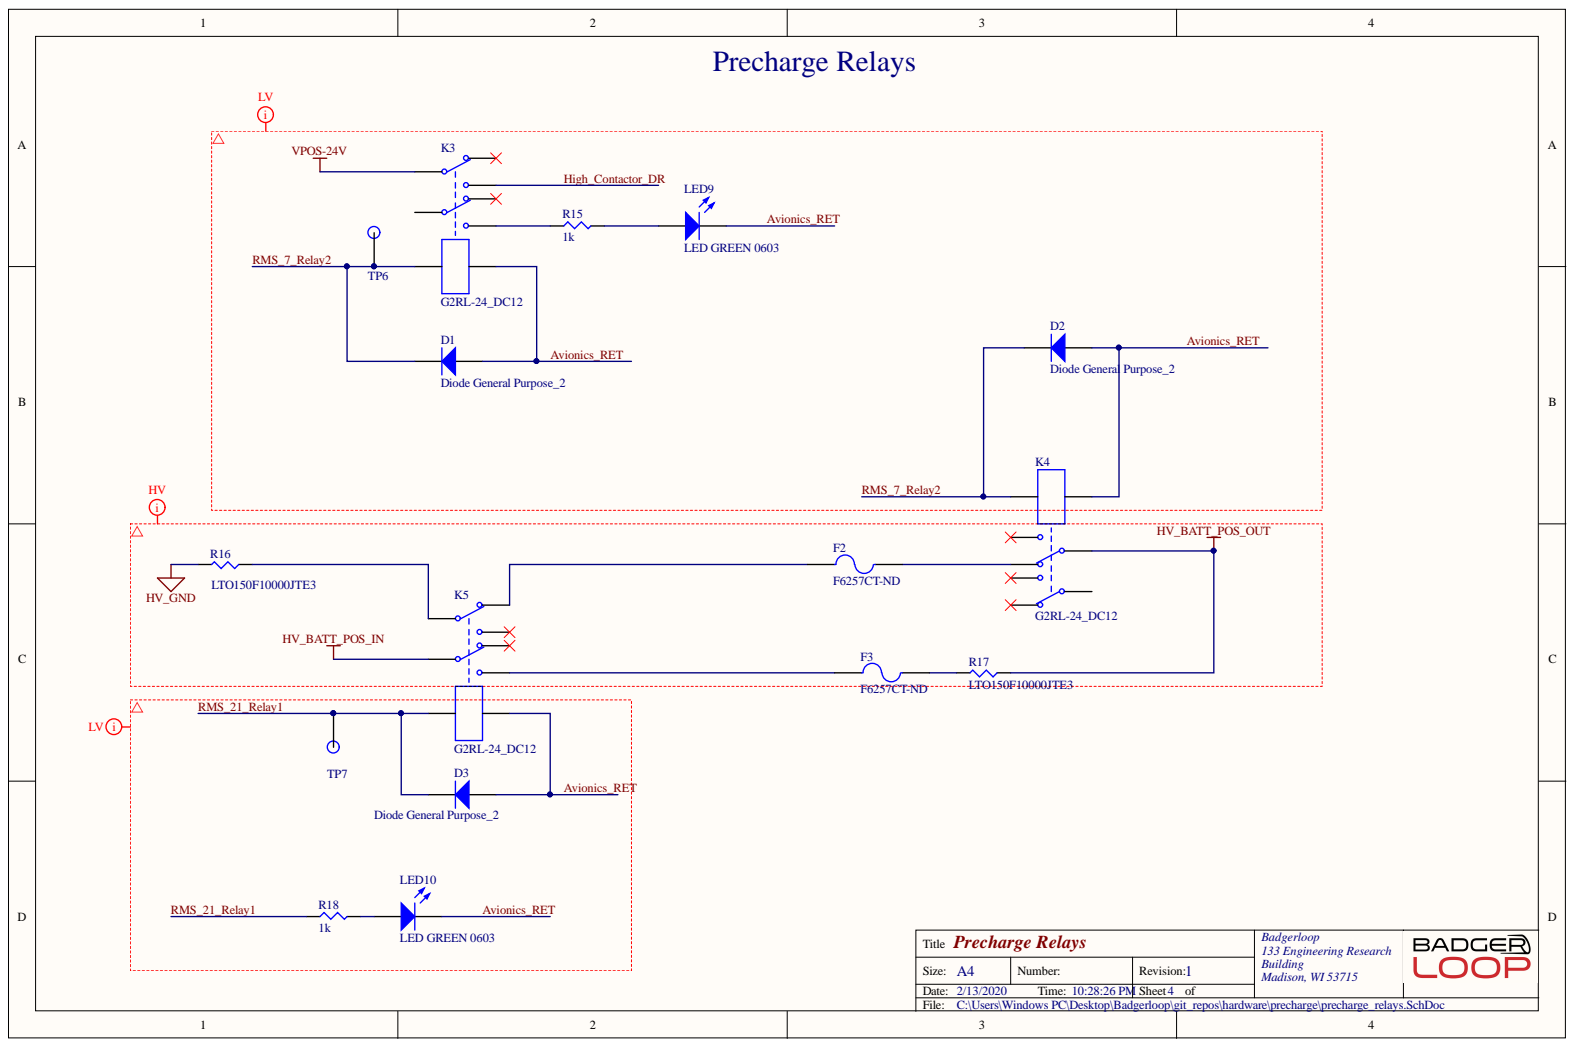
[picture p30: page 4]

Precharge Relays Title | Badgerloop 133 Engineering Research Building Madison, WI 53715

A4 Size: | Number: | 1 Revision:

Date: 2/13/2020 Time: 10:28:26 PM | | Sheet 4 of
File: C:\Users\Windows PC\Desktop\Badgerloop\git_repos\hardware\precharge\precharge_relays.SchDoc

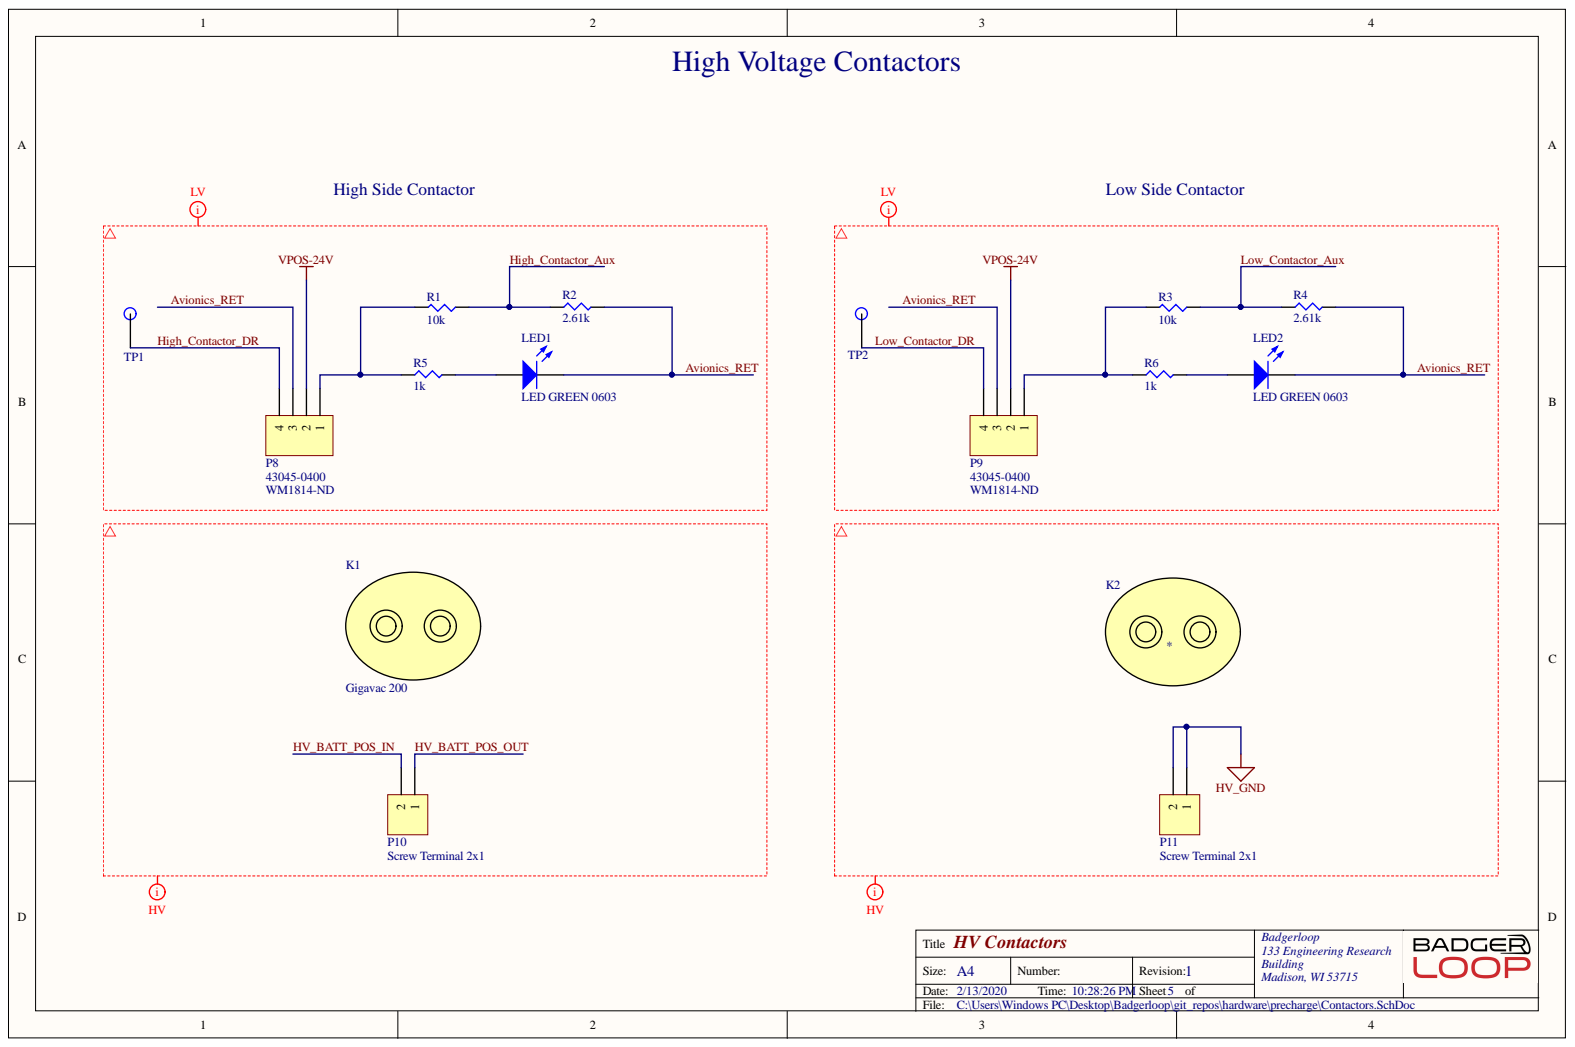
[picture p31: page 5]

HV Contactors Title | Badgerloop 133 Engineering Research Building Madison, WI 53715

A4 Size: | Number: | 1 Revision:

Date: 2/13/2020 Time: 10:28:26 PM | | Sheet 5 of
File: C:\Users\Windows PC\Desktop\Badgerloop\git_repos\hardware\precharge\Contactors.SchDoc






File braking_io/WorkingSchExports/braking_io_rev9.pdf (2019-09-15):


Title Braking IO PCB | Badgerloop Electrical 133 Engineering Research Building 1500 Engineering Drive Madison, Wi 53706

Engineer: | Revision:
Date: 9/14/2019 Time: 11:10:59 PM | Sheet of
File: braking_io.SchDoc


should change upstream fuse to be higher current rating than downstream.

Size L4 for max input current (9A)

Max current draw: 9A -> 9A*0.01Ohm=0.09V
INA Gain: 200V/V -> 4.0V at Max current
Power: I^2*R=4A*0.01=0.04W

Filter design reference: http://www.ti.com/lit/an/snva538/snva538.pdf
http://ecee.colorado.edu/~rwe/papers/APEC99.pdf

Max current draw: 9A -> 9A*0.002Ohm=0.018V
INA Gain: 200V/V -> 3.6V at Max current

Title Bus Filter | Badgerloop Electrical 133 Engineering Research Building 1500 Engineering Drive Madison, Wi 53706

Engineer: | Revision:
Date: 9/14/2019 Time: 11:10:59 PM | Sheet of
File: bus_filter.SchDoc


HRN_UART_DRV_1

MAIN_HB_IN

HRN_VBUS_DRV_1

SOLENOIDS Split into 2 connectors as only 4 solenoids are likely to be used

Title Connectors | Badgerloop Electrical 133 Engineering Research Building 1500 Engineering Drive Madison, Wi 53706

Fiducals Place on corners of board

Mount Holes Avoid routing under screw head

Engineer: | Revision:
Date: 9/14/2019 Time: 11:10:59 PM | Sheet of
File: connectors.SchDoc


NRST pull to GND to Reset, Float Otherwise

I2C2_SDA
I2C2_SCL
MCU_HB_IN

If pull up DNP, address pulled down per datasheet

Title Microcontroller | Badgerloop Electrical 133 Engineering Research Building 1500 Engineering Drive Madison, Wi 53706

Engineer: | Revision:
Date: 9/14/2019 Time: 11:11:00 PM | Sheet of
File: mcu.SchDoc


Title Power 24V | Badgerloop Electrical 133 Engineering Research Building 1500 Engineering Drive Madison, Wi 53706

Engineer: | Revision:
Date: 9/14/2019 Time: 11:11:00 PM | Sheet of
File: power_24V.SchDoc


Notes:
Follow layout reference design
Place bypass caps close to regulator
Keep hot loops as short as possible
Possible to replace ceramic bulk cap with a tantalum.

Replace with Tantalum?
Place close to regulator
See https://github.com/badgerloop-software/hardware/tree/master/braking_io/design

VIN MIN: 8V VIN MAX: 35V
IOUT MAX: Up to 2A
VOUT=(R1*1.221)/(R2)+1.221
VOUT=(10K*1.221)/(3.24K)+1.221=4.989V nominal

Keep SNS route short and fat!

Max current draw: 2A -> 2A*0.01Ohm=0.02V
INA Gain: 200V/V -> 4.0V at Max current
Power: I^2*R=4A*0.01=0.04W

GAIN: 1.6 -> MAX ADC VOLTAGE 4.0V

Title Power 5V | Badgerloop Electrical 133 Engineering Research Building 1500 Engineering Drive Madison, Wi 53706

Engineer: | Revision:
Date: 9/14/2019 Time: 11:11:00 PM | Sheet of
File: power_5V.SchDoc

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

Possible to replace ceramic bulk cap with a tantalum.

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

GND Place close to regulator

VIN MIN: 9V VIN MAX: 35V
IOUT MAX: Up to 2A
VOUT=(R1*1.221)/(R2)+1.221
VOUT=(10K*1.221)/(1.8K)+1.221=V nominal

Keep SNS route short and fat!

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

GAIN: 1.2 -> MAX ADC VOLTAGE 4.20V
VOLTAGE TELEMETRY

Title 7V SUPPLY | Badgerloop Electrical 133 Engineering Research Building 1500 Engineering Drive Madison, Wi 53706

Engineer: | Revision:
Date: 9/14/2019 Time: 11:11:00 PM | Sheet of
File: power_7V.SchDoc


Populate Bottom resistor for current output
Current Min Output: 4mA*200=800mV
Current Max Output: 20mA*200=4.0V
Voltage Min Output: 0.5V
Voltage Max Output: 4.5V

Populate R? for PCB mount temp

Title Pressure Sensors | Badgerloop Electrical 133 Engineering Research Building 1500 Engineering Drive Madison, Wi 53706

Engineer: | Revision:


nFault 5

Check 100k | V-BUS_SOL

Title Solenoids | Badgerloop Electrical 133 Engineering Research Building 1500 Engineering Drive Madison, Wi 53706

Engineer: | Revision:
Date: 9/14/2019 Time: 11:11:00 PM | Sheet of
File: solenoid.SchDoc


SOL_EN_7 | GPB7 8

V-BUS_SOL | VDD 9

VSS 10

Note: Connect LEDs to Solenoid line externally for easy identification

Title Solenoid Control | Badgerloop Electrical 133 Engineering Research Building 1500 Engineering Drive Madison, Wi 53706
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

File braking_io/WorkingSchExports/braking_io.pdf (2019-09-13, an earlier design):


Title Braking IO PCB | Badgerloop Electrical 133 Engineering Research Building 1500 Engineering Drive Madison, Wi 53706

Engineer: | Revision:
Date: 9/13/2019 Time: 6:40:58 PM | Sheet of
File: braking_io.SchDoc


should change upstream fuse to be higher current rating than downstream.

Size L4 for max input current (9A)

Max current draw: 9A -> 9A*0.01Ohm=0.09V
INA Gain: 200V/V -> 4.0V at Max current
Power: I^2*R=4A*0.01=0.04W

Filter design reference: http://www.ti.com/lit/an/snva538/snva538.pdf
http://ecee.colorado.edu/~rwe/papers/APEC99.pdf

Max current draw: 9A -> 9A*0.002Ohm=0.018V
INA Gain: 200V/V -> 3.6V at Max current

Title Bus Filter | Badgerloop Electrical 133 Engineering Research Building 1500 Engineering Drive Madison, Wi 53706

Engineer: | Revision:
Date: 9/13/2019 Time: 6:40:58 PM | Sheet of
File: bus_filter.SchDoc


HRN_UART_DRV_1

MAIN_HB_IN

HRN_VBUS_DRV_1

SOLENOIDS Split into 2 connectors as only 4 solenoids are likely to be used

Title Connectors | Badgerloop Electrical 133 Engineering Research Building 1500 Engineering Drive Madison, Wi 53706

Fiducals Place on corners of board

Mount Holes Avoid routing under screw head

Engineer: | Revision:
Date: 9/13/2019 Time: 6:40:58 PM | Sheet of
File: connectors.SchDoc


NRST pull to GND to Reset, Float Otherwise

I2C2_SDA
I2C2_SCL
MCU_HB_IN

If pull up DNP, address pulled down per datasheet

Title Microcontroller | Badgerloop Electrical 133 Engineering Research Building 1500 Engineering Drive Madison, Wi 53706

Engineer: | Revision:
Date: 9/13/2019 Time: 6:40:58 PM | Sheet of
File: mcu.SchDoc


Notes:
Follow layout reference design
Place bypass caps close to regulator
Keep hot loops as short as possible
Possible to replace ceramic bulk cap with a tantalum.

Replace with Tantalum?
Place close to regulator
See https://github.com/badgerloop-software/hardware/tree/master/braking_io/design

VIN MIN: 8V VIN MAX: 35V
IOUT MAX: Up to 2A
VOUT=(R1*1.221)/(R2)+1.221
VOUT=(10K*1.221)/(3.24K)+1.221=4.989V nominal

Keep SNS route short and fat!

Max current draw: 2A -> 2A*0.01Ohm=0.02V
INA Gain: 200V/V -> 4.0V at Max current
Power: I^2*R=4A*0.01=0.04W

GAIN: 1.6 -> MAX ADC VOLTAGE 4.0V

Title | Badgerloop Electrical 133 Engineering Research Building 1500 Engineering Drive Madison, Wi 53706

Engineer: | Revision:
Date: 9/13/2019 Time: 6:40:58 PM | Sheet of
File: power_5V.SchDoc

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

Possible to replace ceramic bulk cap with a tantalum.

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

GND Place close to regulator

VIN MIN: 9V VIN MAX: 35V
IOUT MAX: Up to 2A
VOUT=(R1*1.221)/(R2)+1.221
VOUT=(10K*1.221)/(1.8K)+1.221=V nominal

Keep SNS route short and fat!

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

GAIN: 1.2 -> MAX ADC VOLTAGE 4.20V
VOLTAGE TELEMETRY

Title 7V SUPPLY | Badgerloop Electrical 133 Engineering Research Building 1500 Engineering Drive Madison, Wi 53706

Engineer: | Revision:
Date: 9/13/2019 Time: 6:40:59 PM | Sheet of
File: power_7V.SchDoc


Populate Bottom resistor for current output
Current Min Output: 4mA*200=800mV
Current Max Output: 20mA*200=4.0V
Voltage Min Output: 0.5V
Voltage Max Output: 4.5V

Populate R? for PCB mount temp

Title Pressure Sensors | Badgerloop Electrical 133 Engineering Research Building 1500 Engineering Drive Madison, Wi 53706

Engineer: | Revision:


nFault 5

Check 100k | V-BUS_SOL

Title Solenoids | Badgerloop Electrical 133 Engineering Research Building 1500 Engineering Drive Madison, Wi 53706

Engineer: | Revision:
Date: 9/13/2019 Time: 6:40:59 PM | Sheet of
File: solenoid.SchDoc


SOL_EN_7 | GPB7 8

V-BUS_SOL | VDD 9

VSS 10

Note: Connect LEDs to Solenoid line externally for easy identification

Title Solenoid Control | Badgerloop Electrical 133 Engineering Research Building 1500 Engineering Drive Madison, Wi 53706

Engineer: | Revision:
Date: 9/13/2019 Time: 6:41:00 PM | Sheet of
File: solenoid_drv.SchDoc


SDA 2
SCL 3
GND 4
V+ 5

ADC_INT_0 | nINT 6

ADC_INT_1 | nINT 6
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

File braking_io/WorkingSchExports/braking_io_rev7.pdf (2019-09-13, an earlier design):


Title Braking IO PCB | Badgerloop Electrical 133 Engineering Research Building 1500 Engineering Drive Madison, Wi 53706

Engineer: | Revision:
Date: 9/12/2019 Time: 12:59:03 PM | Sheet of
File: braking_io.SchDoc


should change upstream fuse to be higher current rating than downstream.

Size L4 for max input current (9A)

Max current draw: 9A -> 9A*0.01Ohm=0.09V
INA Gain: 200V/V -> 4.0V at Max current
Power: I^2*R=4A*0.01=0.04W

Filter design reference: http://www.ti.com/lit/an/snva538/snva538.pdf
http://ecee.colorado.edu/~rwe/papers/APEC99.pdf

Max current draw: 9A -> 9A*0.002Ohm=0.018V
INA Gain: 200V/V -> 3.6V at Max current

Title | Badgerloop Electrical 133 Engineering Research Building 1500 Engineering Drive Madison, Wi 53706

Engineer: | Revision:
Date: 9/12/2019 Time: 12:59:03 PM | Sheet of
File: bus_filter.SchDoc


HRN_UART_DRV_1

MAIN_HB_IN

HRN_VBUS_DRV_1

SOLENOIDS Split into 2 connectors as only 4 solenoids are likely to be used

TODO UPDATE TO 24 PIN

Title Connectors | Badgerloop Electrical 133 Engineering Research Building 1500 Engineering Drive Madison, Wi 53706

Fiducals Place on four corners of board

Mount Holes Avoid routing under screw head

Engineer: | Revision:
Date: 9/12/2019 Time: 12:59:03 PM | Sheet of
File: connectors.SchDoc


NRST pull to GND to Reset, Float Otherwise

I2C2_SDA
I2C2_SCL
MCU_HB_IN

A2 3 | GND

HRN_VBUS_DRV_1

Title Microcontroller | Badgerloop Electrical 133 Engineering Research Building 1500 Engineering Drive Madison, Wi 53706

Engineer: | Revision:
Date: 9/12/2019 Time: 12:59:03 PM | Sheet of
File: mcu.SchDoc


Notes:
Follow layout reference design
Place bypass caps close to regulator
Keep hot loops as short as possible
Possible to replace ceramic bulk cap with a tantalum.

Replace with Tantalum?
Place close to regulator
See https://github.com/badgerloop-software/hardware/tree/master/braking_io/design

VIN MIN: 8V VIN MAX: 35V
IOUT MAX: Up to 2A
VOUT=(R1*1.221)/(R2)+1.221
VOUT=(10K*1.221)/(3.24K)+1.221=4.989V nominal

Keep SNS route short and fat!

Max current draw: 2A -> 2A*0.01Ohm=0.02V
INA Gain: 200V/V -> 4.0V at Max current
Power: I^2*R=4A*0.01=0.04W

GAIN: 1.6 -> MAX ADC VOLTAGE 4.0V

Title | Badgerloop Electrical 133 Engineering Research Building 1500 Engineering Drive Madison, Wi 53706

Engineer: | Revision:
Date: 9/12/2019 Time: 12:59:03 PM | Sheet of
File: power_5V.SchDoc

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

VIN MIN: 9V VIN MAX: 35V
IOUT MAX: Up to 2A
VOUT=(R1*1.221)/(R2)+1.221
VOUT=(10K*1.221)/(1.8K)+1.221=V nominal

Keep SNS route short and fat!

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

GAIN: 1.2 -> MAX ADC VOLTAGE 4.20V
VOLTAGE TELEMETRY

Title 7V SUPPLY | Badgerloop Electrical 133 Engineering Research Building 1500 Engineering Drive Madison, Wi 53706

Engineer: | Revision:
Date: 9/12/2019 Time: 12:59:04 PM | Sheet of
File: power_7V.SchDoc


Populate Bottom resistor for current output
Current Min Output: 4mA*200=800mV
Current Max Output: 20mA*200=4.0V
Voltage Min Output: 0.5V
Voltage Max Output: 4.5V

Populate R? for PCB mount temp

Title Pressure Sensors | Badgerloop Electrical 133 Engineering Research Building 1500 Engineering Drive Madison, Wi 53706

Engineer: | Revision:
Date: 9/12/2019 Time: 12:59:04 PM | Sheet of
File: pressure.SchDoc


nFault 5

Check 100k | V-BUS_SOL

Title Solenoids | Badgerloop Electrical 133 Engineering Research Building 1500 Engineering Drive Madison, Wi 53706

Engineer: | Revision:
Date: 9/12/2019 Time: 12:59:04 PM | Sheet of
File: solenoid.SchDoc


SOL_EN_7 | GPB7 8

V-BUS_SOL | VDD 9

VSS 10

Title Solenoid Control | Badgerloop Electrical 133 Engineering Research Building 1500 Engineering Drive Madison, Wi 53706

Engineer: | Revision:
Date: 9/12/2019 Time: 12:59:04 PM | Sheet of
File: solenoid_drv.SchDoc


SDA 2
SCL 3
GND 4
V+ 5

ADC_INT_0 | nINT 6

ADC_INT_1 | nINT 6

Title | Badgerloop Electrical 133 Engineering Research Building 1500 Engineering Drive Madison, Wi 53706
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

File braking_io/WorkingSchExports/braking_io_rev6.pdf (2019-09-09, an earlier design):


Title Braking IO PCB | Badgerloop Electrical 133 Engineering Research Building 1500 Engineering Drive Madison, Wi 53706

Engineer: | Revision:
Date: 9/9/2019 Time: 2:18:58 PM | Sheet of
File: braking_io.SchDoc


should change upstream fuse to be higher current rating than downstream.

Size L4 for max input current (9A)

Max current draw: 9A -> 9A*0.01Ohm=0.09V
INA Gain: 200V/V -> 4.0V at Max current
Power: I^2*R=4A*0.01=0.04W

Filter design reference: http://www.ti.com/lit/an/snva538/snva538.pdf
http://ecee.colorado.edu/~rwe/papers/APEC99.pdf

Max current draw: 9A -> 9A*0.002Ohm=0.018V
INA Gain: 200V/V -> 3.6V at Max current

Title | Badgerloop Electrical 133 Engineering Research Building 1500 Engineering Drive Madison, Wi 53706

Engineer: | Revision:
Date: 9/9/2019 Time: 2:18:58 PM | Sheet of
File: bus_filter.SchDoc


HRN_UART_DRV_1

MAIN_HB_IN

HRN_VBUS_DRV_1

SOLENOIDS Split into 2 connectors as only 4 solenoids are likely to be used

TODO UPDATE TO 24 PIN

Title Connectors | Badgerloop Electrical 133 Engineering Research Building 1500 Engineering Drive Madison, Wi 53706

Fiducals Place on four corners of board

Mount Holes Avoid routing under screw head

Engineer: | Revision:
Date: 9/9/2019 Time: 2:18:58 PM | Sheet of
File: connectors.SchDoc


NRST pull to GND to Reset, Float Otherwise

I2C2_SDA
I2C2_SCL
MCU_HB_IN

Fixed output, 1A Max (MCU 800mA Max)

A2 3 | GND

HRN_VBUS_DRV_1

Title Microcontroller | Badgerloop Electrical 133 Engineering Research Building 1500 Engineering Drive Madison, Wi 53706

Engineer: | Revision:
Date: 9/9/2019 Time: 2:18:58 PM | Sheet of
File: mcu.SchDoc


Notes:
Follow layout reference design
Place bypass caps close to regulator
Keep hot loops as short as possible
Possible to replace ceramic bulk cap with a tantalum.

Replace with Tantalum?
Place close to regulator
See https://github.com/badgerloop-software/hardware/tree/master/braking_io/design

TODO: Spec new inductor

VIN MIN: 10V VIN MAX: 35V
IOUT MAX: Up to 2A
VOUT=(R1*1.221)/(R2)+1.221
VOUT=(10K*1.221)/(5.76K)+1.221=3.344V nominal

Keep SNS route short and fat!

Max current draw: 2A -> 2A*0.01Ohm=0.02V
INA Gain: 200V/V -> 4.0V at Max current
Power: I^2*R=4A*0.01=0.04W

GAIN: 2.55 -> MAX ADC VOLTAGE 4.21V
VOLTAGE TELEMETRY

Title 3V3 SUPPLY | Badgerloop Electrical 133 Engineering Research Building 1500 Engineering Drive Madison, Wi 53706

Engineer: | Revision:
Date: 9/9/2019 Time: 2:18:58 PM | Sheet of
File: power_3V3.SchDoc

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

TODO: Spec new inductor

VIN MIN: 10V VIN MAX: 35V
IOUT MAX: Up to 2A
VOUT=(R1*1.221)/(R2)+1.221
VOUT=(10K*1.221)/(3.24K)+1.221=4.989V nominal

Keep SNS route short and fat!

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

GAIN: 1.6 -> MAX ADC VOLTAGE 4.0V

Title | Badgerloop Electrical 133 Engineering Research Building 1500 Engineering Drive Madison, Wi 53706

Engineer: | Revision:
Date: 9/9/2019 Time: 2:18:59 PM | Sheet of
File: power_5V.SchDoc


Populate Bottom resistor for current output
Current Min Output: 4mA*200=800mV
Current Max Output: 20mA*200=4.0V
Voltage Min Output: 0.5V
Voltage Max Output: 4.5V

Populate R? for PCB mount temp

Title Pressure Sensors | Badgerloop Electrical 133 Engineering Research Building 1500 Engineering Drive Madison, Wi 53706

Engineer: | Revision:
Date: 9/9/2019 Time: 2:18:59 PM | Sheet of
File: pressure.SchDoc


nFault 5

Check 100k | V-BUS_SOL

Title Solenoids | Badgerloop Electrical 133 Engineering Research Building 1500 Engineering Drive Madison, Wi 53706

Engineer: | Revision:
Date: 9/9/2019 Time: 2:18:59 PM | Sheet of
File: solenoid.SchDoc


SOL_EN_7 | GPB7 8

V-BUS_SOL | VDD 9

VSS 10

Title Solenoid Control | Badgerloop Electrical 133 Engineering Research Building 1500 Engineering Drive Madison, Wi 53706

Engineer: | Revision:
Date: 9/9/2019 Time: 2:18:59 PM | Sheet of
File: solenoid_drv.SchDoc


SDA 2
SCL 3
GND 4
V+ 5

ADC_INT_0 | nINT 6

ADC_INT_1 | nINT 6
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

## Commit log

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2019-09-03 completed solenoids and added watchdog
    [Pressure_Sensors.SchDoc, braking_io.PrjPcb, connectors.SchDoc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]
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2019-09-04 added pressure and thermistors
    [connectors.SchDoc, power.SchDoc, pressure.SchDoc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]
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2019-09-06 added input filter design
    [braking_io.PrjPcb, connectors.SchDoc, mcu.SchDoc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]
2019-09-06 added rail telemetry, updated ADC
    [braking_io.PrjPcb, bus_filter.SchDoc, connectors.SchDoc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]
2019-09-07 added MCU, schematic work
    [braking_io.PrjPcb, bus_filter.SchDoc, connectors.SchDoc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]
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2019-09-08 some cleanup and adding sheets for battery protection
    [battery_protection.PrjPcb, braking_io.PrjPcb, fuse.SchDoc]
2019-09-09 added bypass caps to curr sense
    [braking_io.PrjPcb, bus_filter.SchDoc, connectors.SchDoc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]
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2019-09-10 create battery interface schematic
    [battery_protection.PrjPcb, cell_interface.SchDoc]
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2019-09-13 added bypass caps, fixed 7V line, added LPF on current telemetry
    [bus_filter.SchDoc, connectors.SchDoc, mcu.SchDoc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]
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2019-09-15 Updated braking io files for ESD and misc updates
    [braking_io.PrjPcb, bus_filter.SchDoc]
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2019-09-17 git issue #9 fixes, change MOSFETs, fix nets
    [cell_interface.SchDoc]
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2019-09-25 links to part replacements added
    [cell_interface.SchDoc, ov_uv_dropout.SchDoc]
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2019-09-30 fix libraries and finish indicator light schematic
    [indicator_light.SchDoc, precharge.PrjPcb]
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2019-10-02 update components in battery protection, create precharge connrector, begin precharge schematic
    [cell_interface.SchDoc, connectors.SchDoc, ov_uv_dropout.SchDoc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]
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2019-10-09 finished routing power supplies, cleanup, misc routing. Tuning deisgn rules
    [connectors.SchDoc, mcu.SchDoc, pressure.SchDoc]
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2019-10-09 add new LED to library and add to indicator light schematic
    [Contactors.SchDoc, indicator_light.SchDoc, precharge_relays.SchDoc]
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2019-10-18 finish precharge schematics and footprints with new Wurth components
    [connectors.SchDoc]
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2019-10-20 revert resistor libraries
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2019-10-26 Silkscreen annd DFM fixes
    [braking_io.PrjPcb, bus_filter.SchDoc, connectors.SchDoc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]
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2019-10-26 correct directives and net classes made
    [Contactors.SchDoc, connectors.SchDoc, indicator_light.SchDoc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]
2019-10-29 add holes for right angle contactor just in case
    [precharge_relays.SchDoc]
2019-10-29 fix compliation errors
    [Contactors.SchDoc, connectors.SchDoc, precharge_relays.SchDoc]
2019-10-29 fix resistor libraries to original
    [braking_io.PrjPcb, precharge.PcbDoc]
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2019-10-31 smaller contactor footprint and shrink board layout size
    [indicator_light.SchDoc, precharge.PcbDoc]
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2019-11-04 fix braking io conflict
    [braking_io.PrjPcb]
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2019-11-06 add footprint fix library
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2019-11-06 fix fuse footprint, change out contactors to GV200, add connectors and screw terminals for control
    [Contactors.SchDoc, precharge.PrjPcb, precharge_relays.SchDoc]
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2019-11-07 update precharge schematics with components in official libraries
    [Contactors.SchDoc, precharge.PrjPcb, precharge_relays.SchDoc]
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2019-11-11 fix diode cathode marker
    [precharge.PcbDoc]
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2019-11-19 complete revisions based on 1st design review, add logos and separation silkscreens
    [indicator_light.SchDoc, precharge.PcbDoc]
2019-11-19 Save all files, add RTC symbol and footprint
    [battery_protection.PrjPcb, braking_io.PrjPcb]
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2019-11-19 fix footprint on 1N4148WQ-7
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2019-11-20 begin RMS interface, add header for charge enable
    [bms_interface.SchDoc]
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2019-11-20 create precharge board interface, create 2A fuse compoonent
    [motor_controller_interface.SchDoc]
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2019-11-30 correct net on charger contactor drive
    [bms_interface.SchDoc]
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2019-12-01 fix 3V battery symbol
    [RTC.SchDoc]
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2019-12-01 change charge and discharge enable net to 1 net
    [bms_interface.SchDoc]
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2019-12-01 add last indicator light, change to 1k current limiting resistors
    [shutdown_circuit.SchDoc]
2019-12-01 switch 1ks to match component on other schematics
    [shutdown_circuit.SchDoc]
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2019-12-01 change RC circuit to match fdbk resistor value
    [shutdown_circuit.SchDoc]
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2019-12-02 thermistor expansion module takes 12V, change power net
    [bms_interface.SchDoc]
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2019-12-04 change reset net name
    [RTC.SchDoc]
2019-12-04 change voltage to 3.3 sense we have it
    [RTC.SchDoc]
2019-12-04 change 3V net name to that on beaglebone
    [RTC.SchDoc]
2019-12-04 remove short from shutdown circuit, add bulk cap for bms, move term resistors
    [bms_interface.SchDoc, can_uart.SchDoc, motor_controller_interface.SchDoc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]
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2019-12-06 add 0 ohm resistors to i2c on GPIO
    [generic.SchDoc]
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2019-12-06 add correct net for prchg_rtn
    [motor_controller_interface.SchDoc]
2019-12-06 change pump power circuit resistor from 1k to 180 ohm
    [motor_controller_interface.SchDoc]
2019-12-06 add correct i2c address info
    [generic.SchDoc]
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2019-12-06 update i2c net name correctly
    [RTC.SchDoc]
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2019-12-06 correct i2c address on ADC
    [arduino_shield.SchDoc]
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2019-12-09 add correct feedback resistors on op amps
    [bus_filter.SchDoc, power_5V.SchDoc]
2019-12-09 add updated libraries to project, replace MAX232 w/ new component, add 5V net to VCC
    [braking_io.PrjPcb, mcu.SchDoc]
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2019-12-09 replace current shunt on 7V line
    [power_7V.SchDoc]
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2019-12-09 add limit switch correct nets
    [connectors.SchDoc, generic.SchDoc]
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2019-12-09 correct thermistor nets on ADC
    [arduino_shield.SchDoc]
2019-12-10 Added harness detection, changed source of capacitors C1,2,3, and moved components to continue routing. Found that there are silk to solder clearance violations on the footpritns for many components.
    [Contactors.SchDoc, connectors.SchDoc, indicator_light.SchDoc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]
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2019-12-11 fix flyback diodes
    [shutdown_circuit.SchDoc]
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2019-12-12 add 5V to op amps, add second component on 7V op amp
    [bus_filter.SchDoc, power_5V.SchDoc, power_7V.SchDoc]
2019-12-17 correct power net names, begin UART
    [beaglebone.SchDoc, bus_filter.SchDoc, can_uart.SchDoc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]
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2019-12-18 change ambient sensor to 3.3, create CAN circuit
    [beaglebone.SchDoc, can_uart.SchDoc, misc_sensors.SchDoc]
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2019-12-18 change 24V reference to 12V, add debug headers to CAN
    [can_uart.SchDoc, misc_sensors.SchDoc]
2020-01-04 made the routes that need to cross from HV to LV
    [precharge.PcbDoc, precharge.PrjPcb, precharge_relays.SchDoc]
2020-01-06 rearranged resistors 1-6 and leds 1-2 in order to route connections from P1 easier
    [precharge.PcbDoc]
2020-01-09 add CAN to main BMS connector and rearrange for 1:1
    [bms_interface.SchDoc]
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2020-01-11 correct power naming convention on all
    [bms_interface.SchDoc, motor_controller_interface.SchDoc]
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2020-01-11 correct voltage net names on shutdown circuit
    [shutdown_circuit.SchDoc]
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2020-01-11 add reset signals to BB
    [beaglebone.SchDoc, retros.SchDoc]
2020-01-11 add port for main switch, add connectors for shutdown, analog, retro circuits
    [battery_interface.SchDoc, connectors.SchDoc]
2020-01-12 add braking IO connectors, add CSplit cap, correct ESD diodes, adjust net names
    [beaglebone.SchDoc, can_uart.SchDoc, connectors.SchDoc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]
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2020-01-13 replace current sense op amp and voltage op amps with correct component
    [bus_filter.SchDoc, power_5V.SchDoc]
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2020-01-15 complete batt_protection, just need new components to put in
    [batt_protection.SchDoc]
2020-01-16 add header to batt protec, add good relay to motor pump
    [batt_protection.SchDoc, motor_controller_interface.SchDoc]
2020-01-16 finished all unrouted routes, stared making polygons in necessary places
    [precharge.PcbDoc]
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2020-01-17 error checking
    [batt_protection.SchDoc, misc_sensors.SchDoc, power_12V.SchDoc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]
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2020-01-17 update op amps and current sense amplifiers and resistors
    [bus_filter.SchDoc, power_5V.SchDoc, power_7V.SchDoc]
2020-01-17 correct pinout on MAX232DWR
    [mcu.SchDoc]
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2020-01-18 add fuse to main bus, create comparator for HB
    [batt_protection.SchDoc, beaglebone.SchDoc, bus_filter.SchDoc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]
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2020-01-18 replace capacitor on 12V
    [power_12V.SchDoc]
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2020-01-18 error resolution
    [adc.SchDoc, beaglebone.SchDoc, bms_interface.SchDoc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]
2020-01-18 add correct footprint to CAN
    [can_uart.SchDoc]
2020-01-18 replace accidental 0402s with bigger
    [beaglebone.SchDoc, limit_switches.SchDoc]
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2020-01-20 changed the silk mask rule clearence from 10 mil to 1mil
    [precharge.PcbDoc]
2020-01-21 replaced TL071CDRs w/ TL072CDRs in PcbDoc
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2020-01-23 Schematic and PCB finished. Only missing outline file
    [breakout_board.GBL, breakout_board.GBO, breakout_board.GBP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]
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2020-01-24 rework to move wheel retro signal
    [beaglebone.SchDoc, gpio.SchDoc, retros.SchDoc]
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2020-01-25 more routing and change resistor sizes on shutdown circuit
    [shutdown_circuit.SchDoc]
2020-01-26 routing save for the day, change resistor on 3.3 led
    [beaglebone.SchDoc]
2020-01-28 fixed errors, only 5 errors left on the board
    [precharge.PcbDoc]
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2020-01-31 update PNP transistor to correct pinout, update schematics with updated component and 1.5M resistor
    [solenoid.SchDoc, solenoid_drv.SchDoc]
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2020-01-31 changed rules to have a 4mm or 160 mil constraint for HV on board
    [precharge.PcbDoc]
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2020-02-04 Finished routing, need to fix 3 rule violations
    [precharge.PcbDoc]
2020-02-05 change silego i2c resistors, move board components around for arduino
    [retros.SchDoc]
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2020-02-14 correct gerbers, add step file
    [precharge.GBL, precharge.GBO, precharge.GBP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]
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2020-02-15 trying to correct gerbers
    [breakout_board.GBL, breakout_board.GBO, breakout_board.GBP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]
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
